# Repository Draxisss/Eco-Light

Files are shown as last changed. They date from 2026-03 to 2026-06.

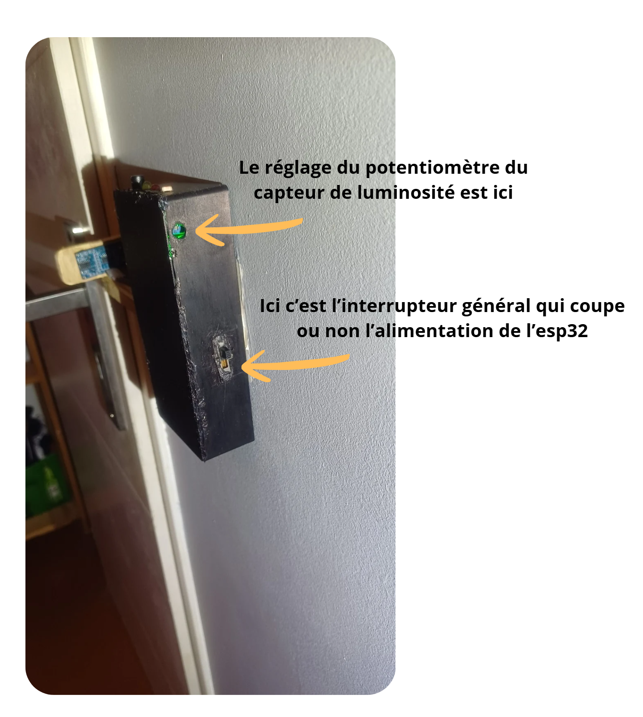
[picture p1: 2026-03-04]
assets/image/lum.png

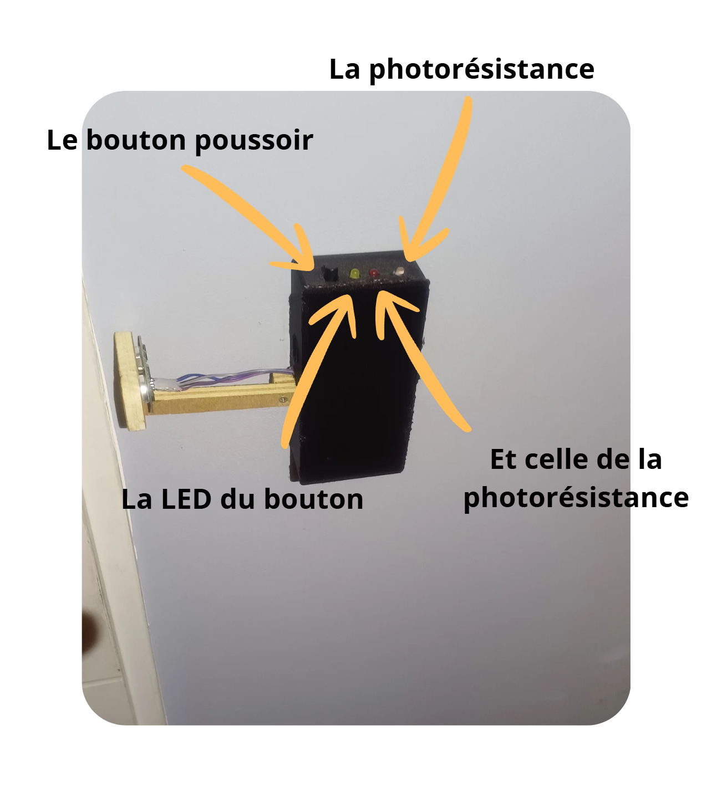
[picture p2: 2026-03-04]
assets/image/comp.png

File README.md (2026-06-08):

# L'Éco'Light 

---

Ceci est ma participation pour le concours Innovez, vous trouverez dans ce dépôt tous les fichiers et explications nécessaires pour comprendre, mettre en place et même juger mon travail si vous faites partie du jury. Voici **l'Éco'Light**.  

La section [montage](#montage) explique comment **vous** pouvez mettre l'Éco'Light chez vous.

## Présentation 

Tout d'abord, l'Éco'Light est un interrupteur autonome et connecté. C'est à dire qu'il remplace un interrupteur classique en lieu et place et surtout dans sa fonction. Pour rapidement voir à quoi il ressemble, il y a la [visualisation 3d](3d/eco-light.stl) 



Lors de la conception de l'Éco'Light, le point de départ était un constat simple : l'interrupteur classique fonctionne bien mais on peut faire **mieux** et quelques limites sont évidentes : le fait d'oublier la lumière allumée en plein jour, ne pas pouvoir allumer les mains prises, l'absence de contrôle à distance et aussi, depuis la crise du Covid-19 où la question de l'hygiène est devenue un sujet central, or l'interrupteur est l'un des objets les plus touchés des espaces partagés, il accumule et transfère donc les microbes. L'Éco'Light est ici une solution parfaite ! Je voulais concevoir l'interrupteur qui réponde à tous ces critères mais aussi qui soit abordable, open-source et fiable, bref qui s'installe comme un interrupteur normal mais fait **bien plus**.

### Contraintes:

- Faire des économies (limiter la possibilité d'allumer la lumière en fonction de la luminosité)
- Pouvoir allumer sans utiliser un bouton physique
- Rendre le tout entièrement connecté et utilisable dans le monde **entier**
- Être compatible au maximum

### Composants, (voir en [détail](#detail-des-composants))

- Le microcontrôleur : un ESP32
- Un capteur à ultrasons : un HC-SR04
- Un relais 5V
- Un module photorésistance
- Un bouton poussoir
- Deux LED (rouge et jaune)

<p align="right">
  
</p>

---

## Fonctionnement

Il suffit d'installer correctement l'Éco'Light à la place de l'interrupteur et via l'application dédiée et ensuite son fonctionnement est très simple : pour changer l'état du plafonnier il faut passer devant le capteur à ultrasons, la distance dépend de ce que l'utilisateur a choisi et la position est ajustable rapidement et à n'importe quel moment.

ultra

En fonction de la luminosité de la pièce, le module photorésistance bloque ou non l'allumage, ou éteint la lumière si elle était allumée lorsque la luminosité a augmenté. Si le module photorésistance est activé alors la LED rouge s'allume pour indiquer à l'utilisateur que le seuil qu'il a fixé est dépassé et qu'il ne peut alors plus allumer la lumière.

lum

On règle ce capteur avec n'importe quel tournevis cruciforme ou plat.

Pour garder la main sur le système le bouton poussoir permet une commande "manuelle", c'est à dire d'allumer ou d'éteindre dans n'importe quelles conditons de luminosité.

comp

### Connectivité 

Faisant partie des contraintes générales qu'en est-il de ce paramètre ?
Et bien un site web permet de surveiller tous les paramètres mais aussi un contrôle total sur le projet **mais pas seulement** on peut aussi avoir accès à d'autres modes de fonctionnement :
- Un mode réveil, qui allume le plafonnier à l'heure choisi
- Un mode cambriolage, qui, si quelque chose passe devant le capteur à ultrasons, envoie une notification et fait clignoter la lumière rapidement
- Un mode plus "fun" que j'ai nommé : mode soirée, qui allume/éteint la lampe au bpm sélectionné



Cette présentation est **personnalisable bien sûr** malgré le fait que ça aurait dû être une application mais j'en reparlerai...

---

### Wiring Diagram 



---
## Composants

| Composant | Quantité |  Prix (EUR) | Lien |
|---|---|---|---|
| Capteur à Ultrasons (HC-SR04) | 1 | 1.40 | https://fr.aliexpress.com/item/1005006039388853.html  |
| Module photorésistance | 1 | 0.94 | https://fr.aliexpress.com/item/1005007038160433.html  |
| Microcontrôleur (ESP32) | 1 | 4.39 | https://fr.aliexpress.com/item/1005008889768599.html |
| Relais | 1 | 1.47 | https://fr.aliexpress.com/item/1005007109343076.html  |
| Bouton poussoir | 1 (20) | 1.31 | https://fr.aliexpress.com/item/4001278311660.html |
| LED | 2 (60) | 2.89 | https://fr.aliexpress.com/item/1005008554748230.html  |
| Interrupteur | 1 (10) | 1.69 | https://fr.aliexpress.com/item/1005007498633815.html  |
| Phase et masse commune | 2 (20) | 1.89 | https://fr.aliexpress.com/item/4000873858801.html |
| Fils de branchements 10cm et 30cm | 40 | 6 en tout | https://fr.aliexpress.com/item/1005002000655439.html  |
| Convertisseur 220v AC vers 5v DC  | 1 | 1.35 | https://fr.aliexpress.com/item/1005001970797548.html  |
| Fils électrique 220v | 1 | 3.59 | https://fr.aliexpress.com/item/1005010779278423.html  |
| Connecteur Wago | 3 | 1.73 | https://fr.aliexpress.com/item/1005006963063019.html  |
| Vis (M4x30, Countersunk head) | 2 (10) | 3.09 | https://fr.aliexpress.com/item/1005007129209802.html  |
| Écrou | 2 (50) | 2.44 | https://fr.aliexpress.com/item/1005010329406193.html  |  
| Résistances | 2 (20) | 0.99 | https://fr.aliexpress.com/item/1005006424279944.html |
| Total | | 35 | C'est seulement si vous achetez toutes les pièces, on peut faire de la récup sur certain composants  |

Pour ma part j'ai réutilisé le convertisseur 220V AC vers 5V DC d'un chargeur, le bouton poussoir d'un petit appareil (PS : un jouet pour enfant, peut-être un dinosaure électronique je ne me souviens plus très bien), les leds d'un jouet pour bébé, les résistances d'un autre projet et les fils d'un starter pack arduino.

**PS :** Les quantités entre parenthèses sont les quantités minimum disponible pour ce produit. Vous pouvez très bien adapter du matériel que vous avez déjà, j'ai simplement mis tout les éléments nécessaires a la conception de l'Éco'Light. Les liens proviennent tous d'aliexpress (plus simple pour l'électronique donc j'ai continué sur ma lancée) mais ils pourront malheureusement devenir invalides si je ne les verifie et actualise pas.
 
### Pour les retrouver vous même : 

- Capteur à Ultrasons : HC-SR04
- Module photorésistance : LDR, module photorésistance, sortie digitale
- Microcontrôleur : ESP32, module devkit, Wi-Fi/Bluetooth
- Relais : module relais, 5 V, 1 canal
- Bouton poussoir : bouton poussoir, 8-10mm, bistable/à verrouillage
- LED : LED 5 mm
- Interrupteur :  2.3 x 0.75 x 1.7cm environ
- Phase et masse commune : Board Pin Header que vous soudez ensemble
- Fils de branchements 10 cm et 30 cm : femelle/femelle
- Convertisseur 220 V → 5 V : module AC-DC, 5w
- Fils électrique 220 V : awg14-15
- Connecteur Wago triple
- Vis : M4x30, tête fraisée
- Écrou : écrou M4, 2-2.5mm d'épaisseur
- Résistance : 150-220Ω

## Montage
Matériel nécessaire : 
- tous les composants
- un tournevis cruciforme
- un fer à souder (aucune soudure n'est difficile)
- un pistolet à colle
- une pince ou quelque chose de similaire et une clé Allen pour les vis du bras
- et un peu d'huile de coude

Une fois toutes les pièces réunies, vous pouvez commencer à construire **votre** Éco'Light ! 

Il vous faudra imprimer en 3d le fichier [suivant](3d/eco-light.stl). **Attention** ne surtout pas imprimer les deux corps, c'est seulement pour choisir entre un interrupteur à gauche ou à droite. De même avec les "bras" pour le capteur à ultrasons, imprimez en un seul, j'ai modélisé 3 tailles : 8, 10 et 12cm.

Il faut ensuite récupérer le [code](code/code_esp32.ino) pour l'ESP32 et le flasher sur votre microcontrôleur via Arduino IDE (un logiciel de programmation pour tout ces petits microcontrôleur)

Réalisez le montage ci-dessous soit directement dans le boîter fraichement imprimé si vous êtes confiant soit sur une breadboard pour être sûr : 

| Nom | Pin | "Complément" |
|---|-----|---|
| Trig | 19  | Vcc + Gnd (capteur à ultrasons) |
| Echo | 18  | " " |
| Led jaune | 33  | Gnd |
| Led rouge | 26  | Gnd |
| Relai | 23  | Vcc + Gnd |
| Photorésistance | 27  | Vcc + Gnd |
| Bouton poussoir | 5 | Gnd |
| Plus généralement : VCC | 5V  | |
| GND | Gnd | |
| | | |

Pour les leds, pensez bien à rajouter une résistance, sinon vous risquez de la griller.

Malheureusement n'ayant aucune connaissance en PCB je n'ai pas pu en faire une mais si ce projet marche je promet qu'elle sortira et alors on gagnera en taille de boitier et en facilité de montage.

Une fois que vous êtes sur du bon fonctionnement du projet alors vous pouvez passez au collage où le but va être de tout faire rentrer dans cette petite boîte. La mission peut être un peu technique mais devrait finir par ressembler à ça :

elec

À partir de là vous pouvez passer à la catégorie **installation** pour fixer et démarrer l'Éco'Light.

---
## Installation 

Très simplement vous allez le fixer à la place de l'interrupteur : l'Éco'Light respecte les dimensions standards, entraxe des vis de fixations de 60 mm (boite Ø67 mm).
Il n'y a que le câblage qui change puisqu'il faut alimenter le microcontrôleur en électricité. Rassurez-vous le travail à faire est minime : 



On a donc ça du côté du boitier :



Si on représente tout schématiquement pour mieux comprendre la situation et éclaircir un petit peu les choses 



 Aucune compétence en électricité n'est nécessaire même votre grand-mère pourrait le faire c'est dire ! (ps: je doute que beaucoup de grand-mères utilisent Github).
 Bref plutôt dire qu'il ne faut pas du tout s'inquiéter sur ce point.

 Ensuite vous vissez le tout (2 vis) et il n'y a plus qu'à allumer la machine via l'interrupteur latéral !

 Pour ensuite, magie, vous connecter à l'ESP32 avec votre téléphone pour finaliser la mise en place. Le but de cette application est d'informer le microcontrôleur de vos préférences (mdp wifi, distance détection...), il suffit de suivre ces étapes :

 

 (à chaque fois il y aura la fenêtre d'erreur associée à l'étape correspondante pour comprendre si vous avez un problème)

 Page d'accueil donc, avant il faut appairer l'ESP32 avec votre téléphone (Paramètres → Connexions → Bluetooth → Sélectionner appareil (Éco'Light) → Appairer), après cette étape de complétée et un temps de chargement plus ou moins long :
 

(Le bouton Reset sert si vous avez un problème durant le processus (freeze, erreur...), il redémarre l'ESP32 et vous renvoie à la page d'accueil)

 Vous arrivez sur :

 

Il faut donc choisir son réseau wifi et indiquer le mot de passe pour que l'ESP32 ait accès à internet

Pour ensuite choisir la distance de détection du capteur à ultrasons (votre choix dépendra de l'emplacement de votre interrupteur, de la position de votre capteur mais surtout si vous voulez qu'il vous détecte quand vous passez vous ou votre main. Par exemple je l'ai réglé moi pour que, quand je circule, le capteur ne détecte rien mais quand je me rapproche ou passe ma main devant il allume la lumière (on peut donc rentrer et sortir sans changer l'état de la lumière). C'est plus agréable je trouve surtout si vous vivez à plusieurs, qu'il y a des va et vient dans la pièce concernée car on peut quand même allumer la lumière les bras chargés). 



(Ps : moi comme référence je l'ai donc réglé à 13cm avec un interrupteur plutôt proche du cadre de porte)

Vient ensuite la partie "API", créez un compte sur [Adafruit](https://io.adafruit.com) et rentrez vos informations (le nom d'utilisateur et la clé API peuvent être trouvés en cliquant sur l'icone de clé en haut à droite) et vous les rentrez ensuite ci-dessous :



Il faudra ensuite respecter le tableau suivant lors de la création des feeds et du dashboard sur le site d'adafruit où vous irez ensuite après la mise en place de l'Écolight (à vous de personnaliser votre expérience).

| Fonction | Nom du feed  | Objet associé sur le dashboard |
|---|---|---|
| Gérer l'allumage | lampe | Toggle |
| Gérer le mode cambiolage | cambriolage  | Toggle |
| Gérer le message d'alerte | notif | Text (Show icon avec exclamation-triangle) |
| Gérer le mode réveil | reveil | Toggle |
| Gérer l'heure du réveil | reveil heure | Text |
| Gérer le mode "soirée" | soiree | Toggle |
| Gérer les bpm du mode "soirée"  | soiree bpm | Text |

Pour rentrer l'heure pour le réveil dans le bloc texte le format attendu est le suivant : XX:XX (Ex: 7:15, 12:28, 22:55)



Si tout s'est bien passé alors cette page apparait et vous êtes prêt à utiliser l'Éco'Light pour la première fois !
Maintenant que vous êtes sûr du bon fonctionnement du projet vous pouvez alors coller le couvercle à la colle chaude (un léger filet suffit) et profiter pleinement de votre Éco'Light à la maison.

Si jamais un problème arrive ou vous voulez changer de taille de bras et aussi de distance de détection : relancez l'application et coupez et rallumez l'ESP32

---

Je voulais juste faire un point sur l'interface utilisateur, je trouve le dashboard adafruit très limitant (même moche, faut le dire un jour) et j'avais à la base créé une application beaucoup plus agréable que je veux quand même partager malgré le fait que l'API d'adafruit ne m'a pas permis de trouver une solution (impossible de s'abonner à un feed sur adafruit depuis l'application, pour celles ou ceux qui demenderaient).



Donc voilà quelque chose de beaucoup plus attrayant mais que je n'ai pu finaliser malgré des heures de travail...

---

# Conclusion

Je me suis régalé pendant toute la conception, la création, le travail de recherche, la mise en forme ou encore les soirée passées à retourner dans tous les sens un problème que je n'arrivais pas à résoudre sur ce projet pour enfin aboutir. Je suis tellement heureux de pouvoir arriver le soir chez et de n'avoir plus, dans un coin de ma tête, une petite voix me disant de toujours peaufiner un détail que personne ne verra... Mais finalement en plus de l'aboutissement, ça ne serait pas ça qui compteraient le plus, toutes les galères rencontrées, non ?

J'ai bien sur quelques idées d'amélioration en tête et je serais ravi de vous les partager. En tout cas j'espère (si vous êtes arrivé jusque là) que ce projet vous a plu et j'espère surtout vous avoir convaincu !

PS : je n'ai jamais eu de retour extérieur à ce projet mis à part la famille et des amis proches et je pense que c'est toujours extrêmmement intéressant d'en recevoir. Sentez vous libre de partager vos avis et sentiments.
cameosauvageon@mail.com

[Présentation en vidéo du projet](https://youtu.be/p83ESVzQn0w)

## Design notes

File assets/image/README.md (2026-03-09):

# Disclaimer

---

Les photos présentées sont celles de mon prototype installé fonctionnel mais comme n'ayant pas d'imprimante 3d et vivant dans la France à Macron et bien je n'ai pas pu tout réimprimer en 3d. Par contre tout les fichiers sont bon et permettent la création d'un modèle vraiment fini sans les traces de colle ou autres désagréments.

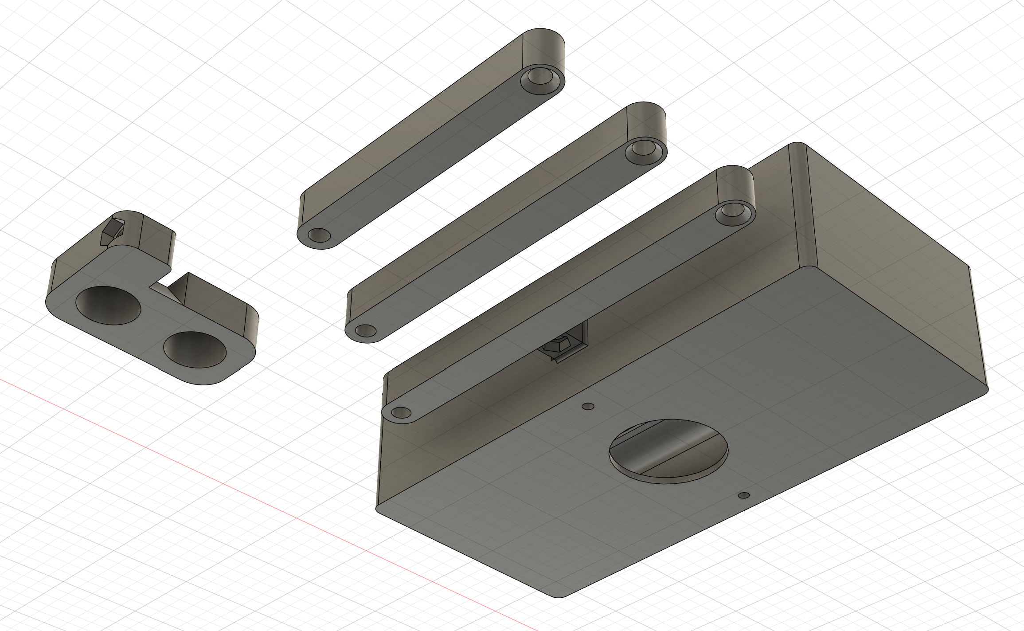
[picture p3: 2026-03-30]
assets/image/Capture d’écran 2026-03-30 215438.png

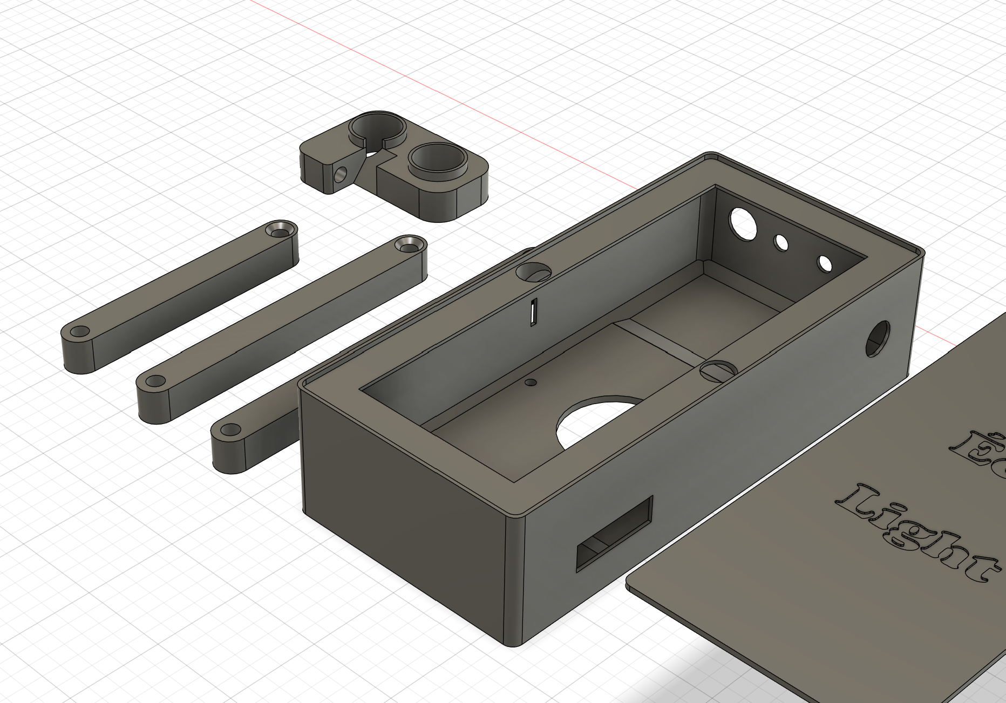
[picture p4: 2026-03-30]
assets/image/Capture d’écran 2026-03-30 215513.png

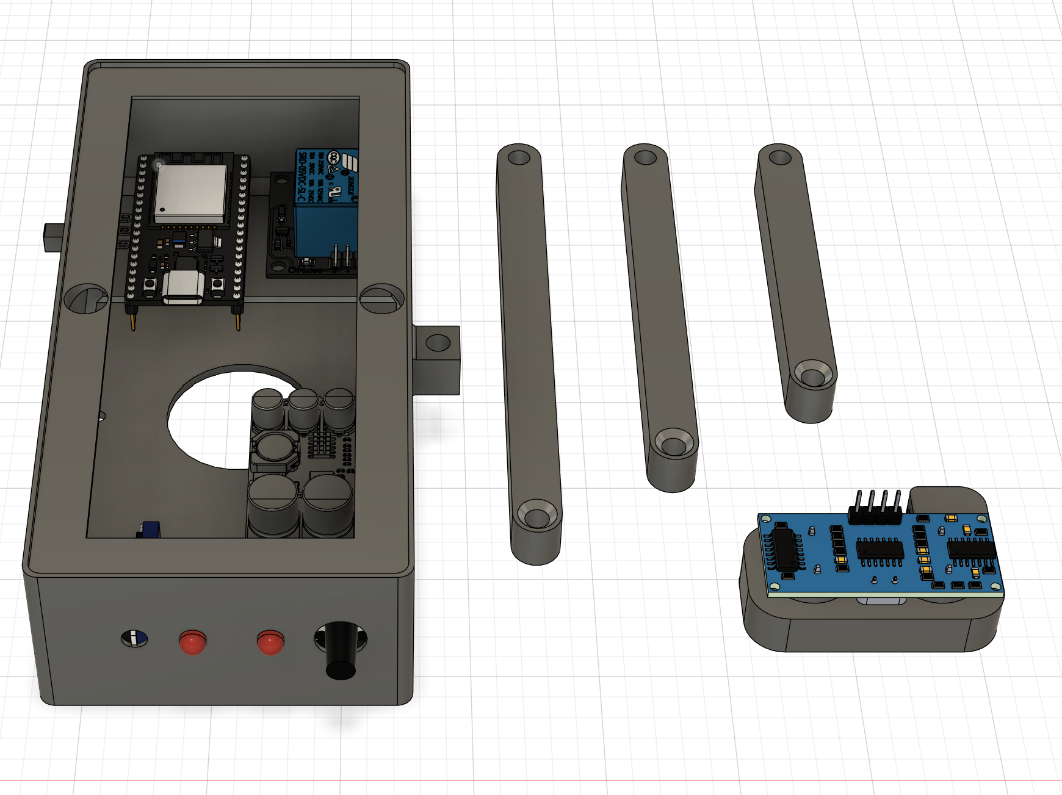
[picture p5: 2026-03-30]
assets/image/Capture d’écran 2026-03-30 232008.png

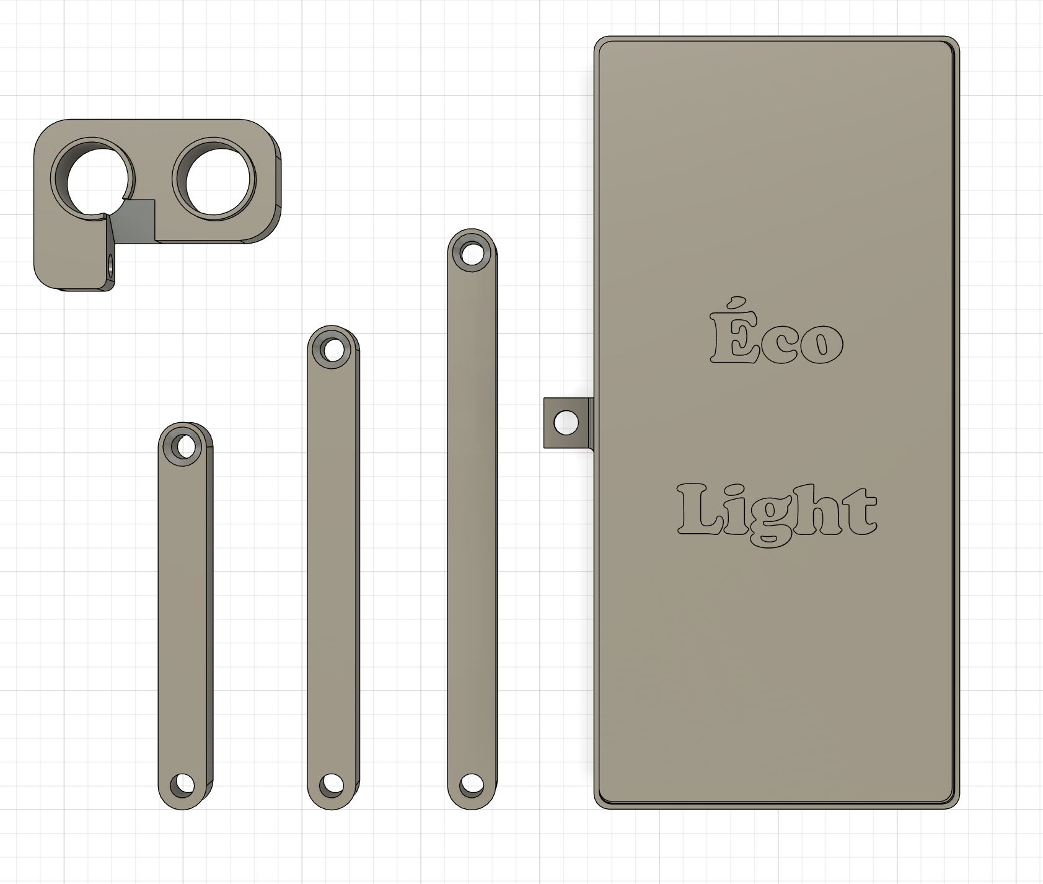
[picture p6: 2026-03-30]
assets/image/Capture d’écran 2026-03-30 215237.png

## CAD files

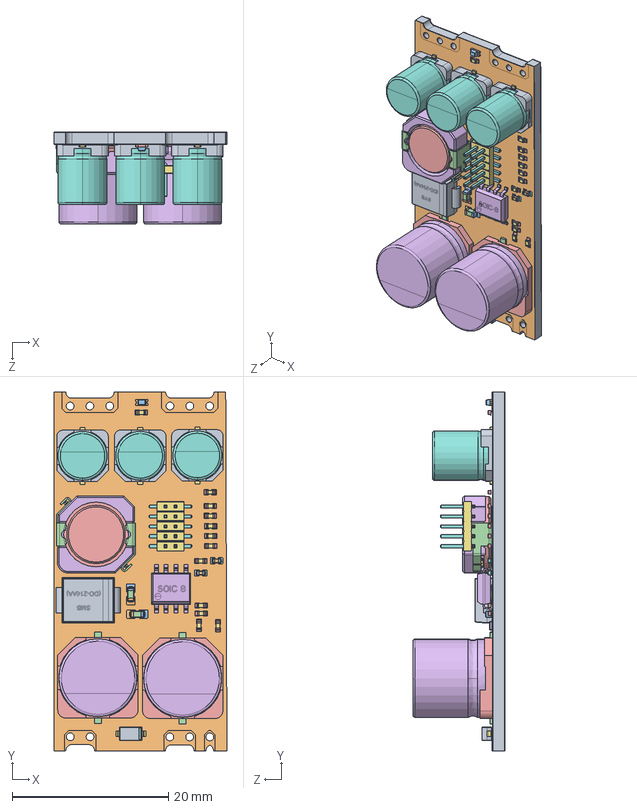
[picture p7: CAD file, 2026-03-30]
assets/Components/Assemblage alim 3 multi choix.STEP
22.2 x 46.0 x 11.9 mm
PCB
Piste face Avant
Piste face Arrière
CAPAE1030X1050N-(G).stp x 2
CAPAE660X800N-(D8).stp x 3
0603 Chip SMD LED (1.6x0.8mm).step
soic8_p1-27_l5-0_w4-0.stp
SOD-123
CDRH104R.step
BaseBody.step
Pin1Body.step
Pin2Body.step
Pin3Body.step
Pin4Body.step
Pin5Body.step
Pin6Body.step
Pin7Body.step
Pin8Body.step
Pin9Body.step
Pin10Body.step
S3M(SMB).step
Cap & pads (1608).step x 2
Pin1.step x 12
Pin2.step x 12
CeramicBody.step x 12
Coating.step x 12
Cap & pads (1005).step x 2

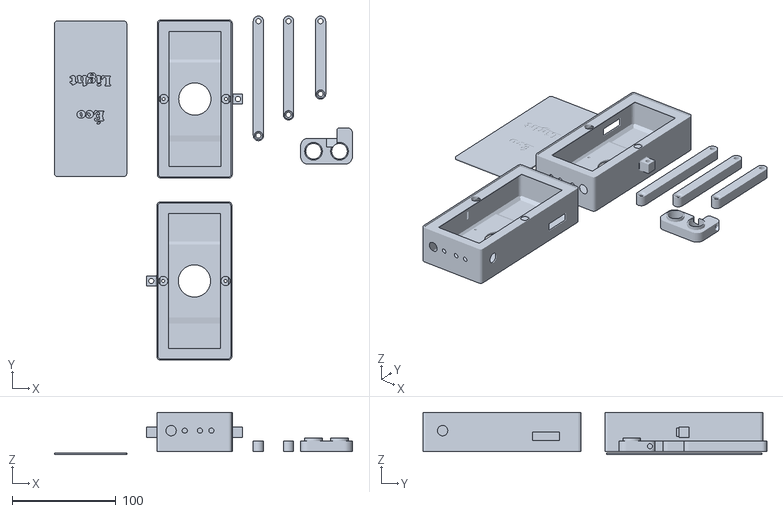
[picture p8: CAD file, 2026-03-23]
3d/eco-light.stl
286.6 x 330.8 x 40.5

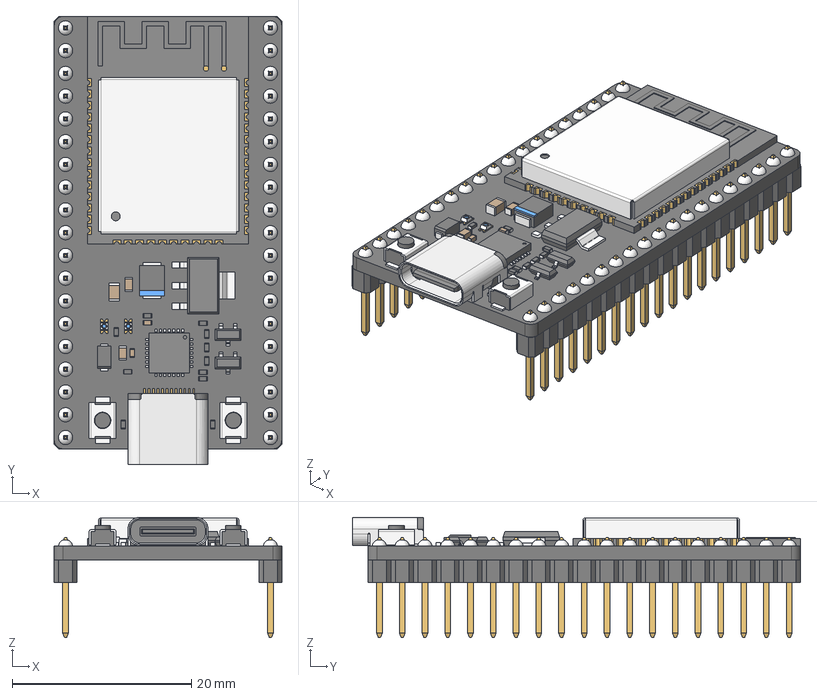
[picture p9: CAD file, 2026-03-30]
assets/Components/ESP32 WROOM.step
25.4 x 50.0 x 13.4 mm

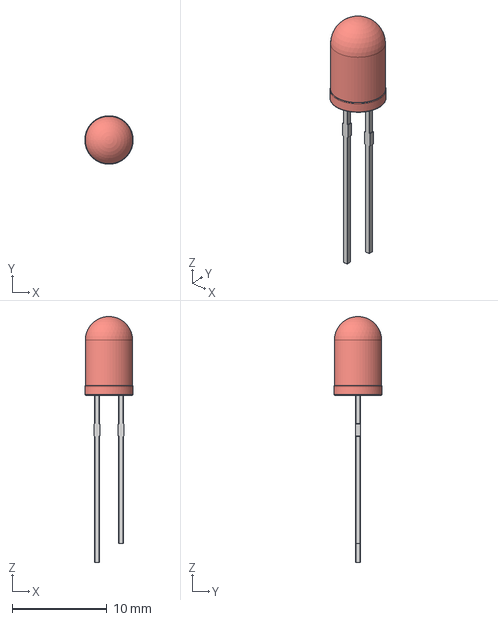
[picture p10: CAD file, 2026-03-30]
assets/Components/LED_5mm.step
5.10 x 5.10 x 25.9 mm

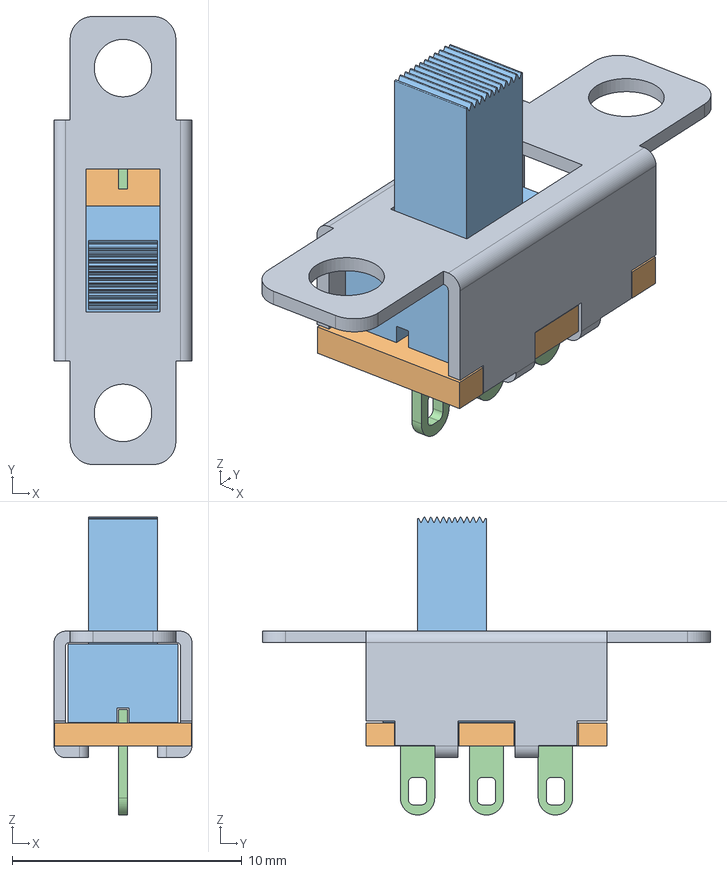
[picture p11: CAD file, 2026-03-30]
assets/Components/switch_SS12F15G5.step
6.00 x 19.5 x 13.0 mm
metal_sw
boad_sw
move_sw
pin_sw
pin_sw001
pin_sw002

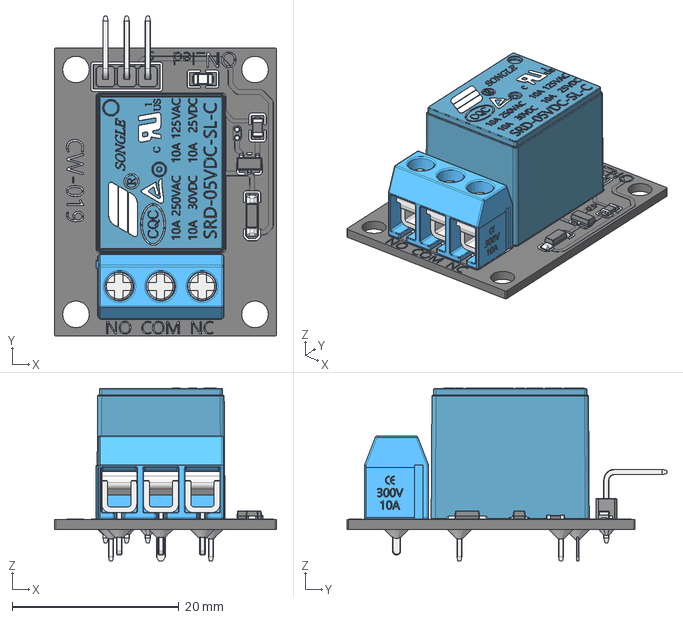
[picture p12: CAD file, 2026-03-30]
assets/Components/CW-019.stp
26.7 x 38.4 x 20.8 mm

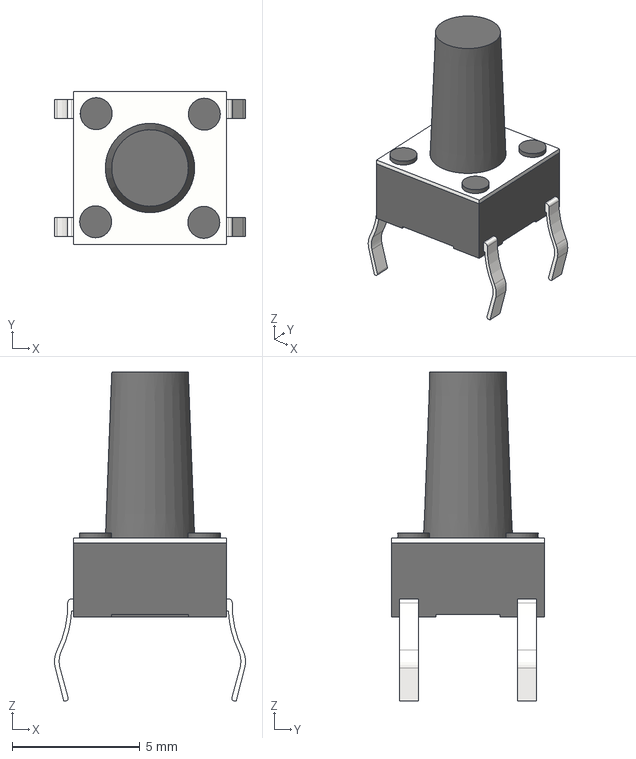
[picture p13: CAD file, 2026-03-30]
assets/Components/push_switch_small.step
7.48 x 6.00 x 12.9 mm

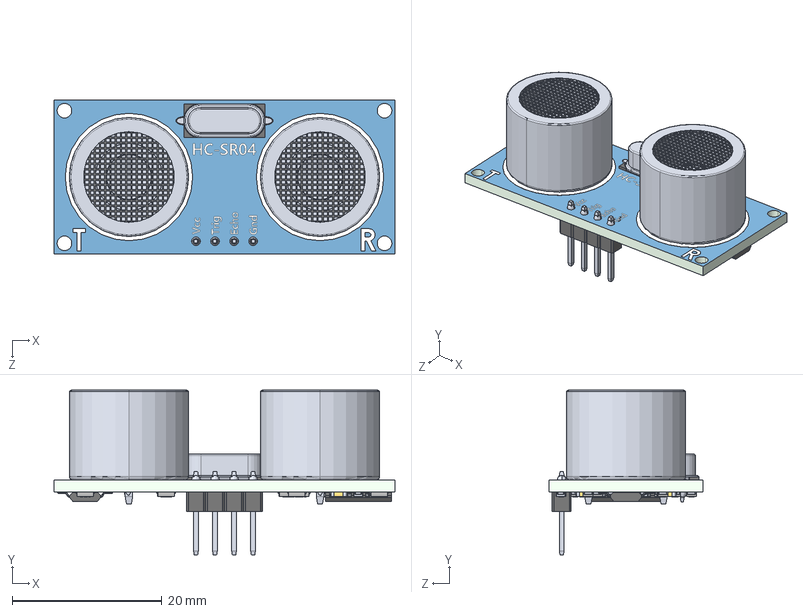
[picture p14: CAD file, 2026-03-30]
assets/Components/HC-SR04.STEP
45.5 x 21.9 x 20.5 mm
HC-SR04board
solder x 10
Emitter x 2
CrystalOscillator
smdChip14pin x 2
smdChip16pin
smdceramiccapacitor x 7
smdResistor753 x 3
smdResistor392
smdResistor103 x 6
smdResistor124 x 2
smdResistor335
smdResistor102
smdResistor563
smdResistor622
smdResistor412
headerMale x 4

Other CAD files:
3d/eco-light_final_with_electronic.f3z
3d/eco-light_fusion360.f3d

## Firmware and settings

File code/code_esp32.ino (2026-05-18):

#include <WiFi.h> 
#include "WiFiClientSecure.h"
#include "Adafruit_MQTT.h"
#include "Adafruit_MQTT_Client.h"
#include "time.h"
#include "BluetoothSerial.h"
#include "Ultrasonic.h"

BluetoothSerial SerialBT;

/************************* adafruit io setup *********************************/

#define AIO_SERVER "io.adafruit.com"
#define AIO_SERVERPORT 1883

WiFiClient client;

char pseudo[50];
char key[50];
Adafruit_MQTT_Client mqtt(&client, AIO_SERVER, AIO_SERVERPORT, pseudo, key);

/****************************** feeds  setup ***************************************/
char path_lampe[60], path_cambriolage[60], path_soiree[60], path_bande_led[60], path_reveil_heure[60], path_soiree_bpm[60], path_notif[60], path_reveil[60];

Adafruit_MQTT_Subscribe lampeSub = Adafruit_MQTT_Subscribe(&mqtt, path_lampe); // cette ligne sert a s'abonner a un feed pour recevoir des donnees via mqtt
Adafruit_MQTT_Publish lampePub = Adafruit_MQTT_Publish(&mqtt, path_lampe); // celle la pour envoyer et ecrire sur un feed

Adafruit_MQTT_Subscribe cambriolageSub = Adafruit_MQTT_Subscribe(&mqtt, path_cambriolage);
Adafruit_MQTT_Publish cambriolagePub = Adafruit_MQTT_Publish(&mqtt, path_cambriolage);

Adafruit_MQTT_Subscribe soireeSub = Adafruit_MQTT_Subscribe(&mqtt, path_soiree);
Adafruit_MQTT_Publish soireePub = Adafruit_MQTT_Publish(&mqtt, path_soiree);

Adafruit_MQTT_Subscribe bande_ledSub = Adafruit_MQTT_Subscribe(&mqtt, path_bande_led);
Adafruit_MQTT_Publish bande_ledPub = Adafruit_MQTT_Publish(&mqtt, path_bande_led);

Adafruit_MQTT_Subscribe reveil_heureSub = Adafruit_MQTT_Subscribe(&mqtt, path_reveil_heure);
Adafruit_MQTT_Publish reveil_heurePub = Adafruit_MQTT_Publish(&mqtt, path_reveil_heure);

Adafruit_MQTT_Subscribe soiree_bpmSub = Adafruit_MQTT_Subscribe(&mqtt, path_soiree_bpm);
Adafruit_MQTT_Publish soiree_bpmPub = Adafruit_MQTT_Publish(&mqtt, path_soiree_bpm);

Adafruit_MQTT_Subscribe notifSub = Adafruit_MQTT_Subscribe(&mqtt, path_notif);
Adafruit_MQTT_Publish notifPub = Adafruit_MQTT_Publish(&mqtt, path_notif);

Adafruit_MQTT_Subscribe reveilSub = Adafruit_MQTT_Subscribe(&mqtt, path_reveil);
Adafruit_MQTT_Publish reveilPub = Adafruit_MQTT_Publish(&mqtt, path_reveil);

/*************************** pins et variables utilisés dans le code ************************************/
bool initialisation1 = false;
bool initialisation2 = false;

// tout les pins 
Ultrasonic ultrasonic1(19, 18); // Trig = 19, Echo = 18
int pin_led = 33;
int pin_bouton = 5;
int pin_led2 = 26;
int pin_relay = 23;
int pin_luminosity = 27;
bool bouton_appuye_previous = false;

//capteur ultrasons
int distance_detection_ultrasonic = 30;
bool etat_lumiere = false;
bool etat_capteur_ultrason = false;
bool interLum = false;
bool interBut = false;
bool varLum = false;
unsigned long lastMqttPing = 0;

// variables qui servent a verifier le precedent message envoyé pour ne pas dépasser la limite par minute de adafruit
const char* etat_lumiere_str_previous = "";
const char* reveil_str_previous = "";
const char* cambriolage_str_previous = "";
const char* soiree_str_previous = "";
const char* bande_led_str_previous = "";

// cambriolage
bool cambriolage = false;
int delay_cambriolage = 500;
unsigned long previous_delay = 0;
bool cambriolageDetect = false;
bool cambriolage_previous = true;
bool notif_state = false;
bool notif_state_previous = false;

bool soiree = false;

bool bande_led = false; // toutes les appellations a bande led sont du parce que je voulais rajouter la possibilité de mettre une bande led en plus du plafonnier principal mais je n'ai pas reussi a flasher un nouveau firmware dans mes bande led donc c'est aussi une partie du projet inachevée

// reveil
bool reveil = false;
bool reveilLum = false;
int reveil_minute = 0;
int reveil_heure = 0;
const char* timezone = "CET-1CEST,M3.5.0/2,M10.5.0/3"; // c'est ce qui gere les passage heure d'hiver/ heure d'ete
const char* ntpServer = "fr.pool.ntp.org";

int soiree_bpm = 100;
int delay_bpm = 60000/soiree_bpm;
unsigned long previous_delay_bpm = 0;

char notif[64] = "";

bool delai = false;

// les fonction callback sont la pour savoir quoi faire quand un nouveau message apparait sur le feed
void lampeCallback(char* message, uint16_t len) {
  char messageBuffer[40];
  snprintf(messageBuffer, sizeof(messageBuffer), "lampe status is :: %s, len :: %u", message, len);
  Serial.println(messageBuffer);
  if (strcmp(message, "ON") == 0) {
    Serial.println("Turning ON lampe");
    digitalWrite(pin_relay, LOW);
    Serial.println("relay on");
    etat_lumiere = true;
  } else {
    Serial.println("Turning OFF lampe");
    digitalWrite(pin_relay, HIGH);
    Serial.println("relay off");
    etat_lumiere = false;
  }
}

void cambriolageCallback(char* message, uint16_t len) {
  char messageBuffer[40];
  snprintf(messageBuffer, sizeof(messageBuffer), "cambriolage status is :: %s, len :: %u", message, len);
  Serial.println(messageBuffer);
  if (strcmp(message, "ON") == 0) {
    cambriolage = true;
  } else {
    cambriolage = false;
  }
}

void soireeCallback(char* message, uint16_t len) {
  char messageBuffer[40];
  snprintf(messageBuffer, sizeof(messageBuffer), "soiree status is :: %s, len :: %u", message, len);
  Serial.println(messageBuffer);
  if (strcmp(message, "ON") == 0) {
    soiree = true;
  } else {
    soiree = false;
  }
}

void bandeLedCallback(char* message, uint16_t len) {
  char messageBuffer[40];
  snprintf(messageBuffer, sizeof(messageBuffer), "bande led status is :: %s, len :: %u", message, len);
  Serial.println(messageBuffer);
  if (strcmp(message, "ON") == 0) {
    bande_led = true;
  } else {
    bande_led = false;
  }
}

void reveilHeureCallback(char* message, uint16_t len) {
  char messageBuffer[40];
  snprintf(messageBuffer, sizeof(messageBuffer), "reveil heure status is :: %s, len :: %u", message, len);
  Serial.println(messageBuffer);

  sscanf(message, "%d:%d", &reveil_heure, &reveil_minute);
  Serial.print(reveil_heure);
  Serial.print(":");
  Serial.println(reveil_minute);

}

void soireeBpmCallback(char* message, uint16_t len) {
  char messageBuffer[40];
  snprintf(messageBuffer, sizeof(messageBuffer), "soiree bpm status is :: %s, len :: %u", message, len);
  Serial.println(messageBuffer);
  soiree_bpm = atoi(message);
  Serial.println(soiree_bpm);
}

void notifCallback(char* message, uint16_t len) {
  char messageBuffer[64];
  snprintf(messageBuffer, sizeof(messageBuffer), "notif status is :: %s, len :: %u", message, len);
  Serial.println(messageBuffer);


}

void reveilCallback(char* message, uint16_t len) {
  char messageBuffer[64];
  snprintf(messageBuffer, sizeof(messageBuffer), "reveil status is :: %s, len :: %u", message, len);
  Serial.println(messageBuffer);
  if (strcmp(message, "ON") == 0) {
    reveil = true;
  } else {
    reveil = false;
  }

}

// la fonction qui permet de publier surles feed sans depasser les limite de message par minute
void indicatorPublish() {

  const char* etat_lumiere_str = etat_lumiere ? "ON" : "OFF";
  if (strcmp(etat_lumiere_str_previous, etat_lumiere_str) != 0) {
    lampePub.publish(etat_lumiere_str);
    etat_lumiere_str_previous = etat_lumiere_str;
  }

  const char* reveil_str = reveil ? "ON" : "OFF";
  if (strcmp(reveil_str_previous, reveil_str) != 0) {
    reveilPub.publish(reveil_str);
    reveil_str_previous = reveil_str;
  }

  const char* cambriolage_str = cambriolage ? "ON" : "OFF";
  if (strcmp(cambriolage_str_previous, cambriolage_str) != 0) {
    cambriolagePub.publish(cambriolage_str);
    cambriolage_str_previous = cambriolage_str;
  }

  const char* soiree_str = soiree ? "ON" : "OFF";
  if (strcmp(soiree_str_previous, soiree_str) != 0) {
    soireePub.publish(soiree_str);
    soiree_str_previous = soiree_str;
  }

  const char* bande_led_str = bande_led ? "ON" : "OFF";
  if (strcmp(bande_led_str_previous, bande_led_str) != 0) {
    bande_ledPub.publish(bande_led_str);
    bande_led_str_previous = bande_led_str;
  }

}


void MQTT_connect() {
  int8_t ret;
  if (mqtt.connected()) {
    return;
  }
  Serial.print("Connecting to MQTT... ");
  uint8_t retries = 20;
  while ((ret = mqtt.connect()) != 0) {  
    Serial.println(mqtt.connectErrorString(ret));
    Serial.println("Retrying MQTT connection in 5 seconds...");
    mqtt.disconnect();
    delay(2000); 
    retries--;
    if (retries == 0) {
      SerialBT.print("XJ");
      esp_restart();
    }
  }
  Serial.println("MQTT Connected!");
}


void setup() {
  Serial.begin(115200);
  delay(10);
  pinMode(pin_led, OUTPUT); 
  pinMode(pin_led2, OUTPUT);
  pinMode(pin_relay, OUTPUT);
  pinMode(pin_luminosity, INPUT);
  pinMode(pin_bouton, INPUT_PULLUP); //assignation des modes aux pins

  Serial.println(F("Concours Innovez version finale"));

  // connecter au wifi
  SerialBT.begin("Eco'light");  // Nom visible en Bluetooth
  
  WiFi.mode(WIFI_STA);
  WiFi.disconnect();
  delay(100);
  Serial.println();

  // Attacher les fonctions de callback
  lampeSub.setCallback(lampeCallback);
  cambriolageSub.setCallback(cambriolageCallback);
  soireeSub.setCallback(soireeCallback);
  bande_ledSub.setCallback(bandeLedCallback);
  reveil_heureSub.setCallback(reveilHeureCallback);
  soiree_bpmSub.setCallback(soireeBpmCallback);
  notifSub.setCallback(notifCallback);
  reveilSub.setCallback(reveilCallback);

}

// boucle principale
void loop() {
  if (SerialBT.hasClient()) {
    if (!initialisation1) {
      Serial.println("Scan start");
      // WiFi.scanNetworks retourne le nombre de réseau trouvé.
      int n = WiFi.scanNetworks();
      Serial.println("Scan done");
      delay(1000);
      for (int i = 0; i < n; ++i) {
        String ssid = WiFi.SSID(i);
        int len = ssid.length();

        // convertir la longueur en chaîne de 2 chiffres
        if (len < 10) {
          SerialBT.print("0");  // ajouter un 0 devant
        }
        SerialBT.print(len);     // envoyer la longueur (ex : "05")
        Serial.println(len);
        delay(500);
        SerialBT.print(ssid);    // puis le SSID brut
        Serial.println(ssid);
        delay(500);
        Serial.println(i);
      }
      SerialBT.print("EN");
      Serial.println("EN");
      WiFi.scanDelete();
      initialisation1 = true;
      }
    }
    
      
    if (SerialBT.available()) {
      if (!initialisation2) {

        String ssid = SerialBT.readStringUntil('\n');
        ssid.trim();  // supprime les espaces ou retours à la ligne
        // on vérifie si le premier caractère est '/'
        if (ssid.length() > 0 && ssid.charAt(0) == '/') {
        ssid.remove(0, 1); // supprime le premier caractère
        }

        Serial.println();
        Serial.print("Connecting to ");
        Serial.println(ssid);

        while (!SerialBT.available()) {
          delay(10);
        }
        String password = SerialBT.readStringUntil('\n');
        password.trim();

        Serial.print("Password: ");
        Serial.println(password);

        // connexion WiFi
        WiFi.begin(ssid.c_str(), password.c_str());

        int attempts = 0;
        while (WiFi.status() != WL_CONNECTED && attempts < 20) {
          delay(500);
          Serial.print(".");
          attempts++;
        }

        if (WiFi.status() == WL_CONNECTED) {
          configTzTime(timezone, ntpServer); // configurer l'heure 
          Serial.println("WiFi connected");
          Serial.println("IP address: ");
          Serial.println(WiFi.localIP()); 
          SerialBT.print("AB");  // confirmer à App Inventor
          digitalWrite(pin_led2, HIGH);
          digitalWrite(pin_led, HIGH);
          delay(1000);
          digitalWrite(pin_led2, LOW);
          digitalWrite(pin_led, LOW);
          delay(500);
          digitalWrite(pin_led2, HIGH);
          digitalWrite(pin_led, HIGH);
          delay(1000);
          digitalWrite(pin_led2, LOW);
          digitalWrite(pin_led, LOW);
          delay(500);
        } else {
          Serial.println("\nÉchec de connexion WiFi.");
          SerialBT.print("XI"); // envoyer l'erreur a App inventor
        }

        while (!SerialBT.available()) {
          delay(10);
        }
        String pseudostr = SerialBT.readStringUntil('\n');
        pseudostr.trim();
        pseudostr.toCharArray(pseudo, sizeof(pseudo));

        snprintf(path_lampe, sizeof(path_lampe), "%s/feeds/lampe", pseudo);
        snprintf(path_cambriolage, sizeof(path_cambriolage), "%s/feeds/cambriolage", pseudo);
        snprintf(path_soiree, sizeof(path_soiree), "%s/feeds/soiree", pseudo);
        snprintf(path_bande_led, sizeof(path_bande_led), "%s/feeds/bande-led", pseudo);
        snprintf(path_reveil_heure, sizeof(path_reveil_heure), "%s/feeds/reveil-heure", pseudo);
        snprintf(path_soiree_bpm, sizeof(path_soiree_bpm), "%s/feeds/soiree-bpm", pseudo);
        snprintf(path_notif, sizeof(path_notif), "%s/feeds/notif", pseudo);
        snprintf(path_reveil, sizeof(path_reveil), "%s/feeds/reveil", pseudo);

        // s'abonner à chaque feed
        mqtt.subscribe(&lampeSub);
        mqtt.subscribe(&cambriolageSub);
        mqtt.subscribe(&soireeSub);
        mqtt.subscribe(&bande_ledSub);
        mqtt.subscribe(&reveil_heureSub);
        mqtt.subscribe(&soiree_bpmSub);
        mqtt.subscribe(&notifSub);
        mqtt.subscribe(&reveilSub);

        while (!SerialBT.available()) {
          delay(10);
        }
        String keystr = SerialBT.readStringUntil('\n');
        keystr.trim();  
        keystr.toCharArray(key, sizeof(key));

        MQTT_connect();

        if (mqtt.connected()) {
          Serial.println("Adafruit connecté");
          Serial.printf("Pseudo: %s | Key: %s\n", pseudo, key);
          SerialBT.print("AC");  // confirmer à App Inventor
          digitalWrite(pin_led2, HIGH);
          digitalWrite(pin_led, LOW);
          delay(1000);
          digitalWrite(pin_led2, LOW);
          digitalWrite(pin_led, HIGH);
          delay(500);
          digitalWrite(pin_led2, HIGH);
          digitalWrite(pin_led, LOW);
          delay(1000);
          digitalWrite(pin_led2, LOW);
          digitalWrite(pin_led, HIGH);
          delay(1000);
          digitalWrite(pin_led2, LOW);
          digitalWrite(pin_led, LOW);
          delay(500);
        } else {
          Serial.println("\nÉchec de connexion MQTT");
          SerialBT.print("XJ"); // envoyer l'echec sinon
        }       

        while (!SerialBT.available()) {
          delay(10);
        }
        String ultra = SerialBT.readStringUntil('\n');
        ultra.trim(); 
        distance_detection_ultrasonic = ultra.toInt(); 

        initialisation2 = true;
      }
    }
  
  if (SerialBT.hasClient()) {
    if (SerialBT.available()) {
      if (SerialBT.read() == 'a') {
        ESP.restart();
      }
    }
  }
  if (initialisation2)  {
    if (WiFi.status() == WL_CONNECTED) {
      MQTT_connect();
      mqtt.processPackets(50);
    } else {
      Serial.println("WiFi non connecté, MQTT ignoré");
    }

    indicatorPublish();

    if (millis() - lastMqttPing >= 10000) {
      lastMqttPing = millis();
      mqtt.ping();
    }
    
/****************************** debut du code pour gerer seulement l'interrupteur et non la connectivite ***************************************/
    delai = false;
    int mesure_ultrasons = ultrasonic1.Ranging(CM);
    bool bouton_appuye = digitalRead(pin_bouton) == LOW; 
    bool luminosite_importante = digitalRead(pin_luminosity) == LOW;

    if (bouton_appuye) {
      interBut = true;
      Serial.println("le bouton est appuyé");
      digitalWrite(pin_led, HIGH);
      if (bouton_appuye != bouton_appuye_previous) {
        bouton_appuye_previous = bouton_appuye;
        delay(250);
      }
    }
    
    if (!bouton_appuye) {
      Serial.println("le bouton est relaché");
      digitalWrite(pin_led, LOW);
      interBut = false;
      if (bouton_appuye == bouton_appuye_previous) {
        bouton_appuye_previous = !bouton_appuye;
        delay(250);
      }
    }  
    
    if (!luminosite_importante) {
      interLum = true;
      digitalWrite(pin_led2, LOW);
    }

    if (luminosite_importante) {
      digitalWrite(pin_led2, HIGH);
      digitalWrite(pin_relay, HIGH);
      Serial.println("la lumiere est trop importante");
      if (!bouton_appuye) {
        etat_lumiere = false;
      }
      interLum = false;

    }
    
    if ((interLum || interBut)&& !soiree) {

      if (mesure_ultrasons < distance_detection_ultrasonic && !cambriolage) {
        etat_capteur_ultrason = true;
      } else if (etat_capteur_ultrason && mesure_ultrasons > distance_detection_ultrasonic) {       //boucle if pour recreer bouton poussoir avec le capteur ultrasons (etat_lumière passe de true a false)
        etat_capteur_ultrason = false;
        etat_lumiere = !etat_lumiere; 
        delai = true;
      }
    }

    if (etat_lumiere) {               //boucle qui gere l'allumage et l'exctinction de la lumière
      digitalWrite(pin_relay, LOW);
      Serial.println("relay on");
    } else {
      digitalWrite(pin_relay, HIGH);
      Serial.println("relay off");
    }

    //********************partie avec les variables de l'application*************************************//

    if (cambriolage) {

      if (mesure_ultrasons < 100) {
        cambriolageDetect = true;
      }

      if (cambriolageDetect) {
        notif_state = true;
        if (millis() - previous_delay > delay_cambriolage) {
          previous_delay = millis();
          digitalWrite(pin_relay, varLum ? HIGH : LOW);
          varLum = !varLum;
        }
      }

      if (notif_state && notif_state != notif_state_previous) {
        notifPub.publish("Attention quelqu'un est passé devant le capteur ultrason");
        notif_state_previous = notif_state;
      }

      cambriolage_previous = true;

    }else{
      notif_state = false;
      cambriolageDetect = false;
      varLum = false;
      notif_state_previous = false;
      if (cambriolage != cambriolage_previous) {
        notifPub.publish("Aucune alerte       ");
        cambriolage_previous = cambriolage;
      }     
    }

    if (bande_led){
    }else{
    }

    int delay_bpm = 60000/soiree_bpm; 

    if (soiree){
      if (millis() - previous_delay_bpm > delay_bpm) {
        previous_delay_bpm = millis();
        digitalWrite(pin_relay, varLum ? HIGH : LOW);
        varLum = !varLum;
      }
    }else{
      varLum = false;
    }

    if (reveil) {
      struct tm timeinfo;
      if (getLocalTime(&timeinfo, 200)) {
        Serial.printf("Date : %02d/%02d/%04d  Heure : %02d:%02d:%02d\n", timeinfo.tm_mday, timeinfo.tm_mon + 1, timeinfo.tm_year + 1900, timeinfo.tm_hour, timeinfo.tm_min, timeinfo.tm_sec);
        if (!reveilLum && timeinfo.tm_hour == reveil_heure && timeinfo.tm_min == reveil_minute) { 
          reveilLum = true;
          digitalWrite(pin_relay, HIGH);
          etat_lumiere = true;
          lampePub.publish("ON");
          Serial.println("relay on par reveil");
        }    
      } else {
        Serial.println("Impossible d'obtenir l'heure via NTP1");
      }
    }else{
      reveilLum = false;
    }
    
    struct tm timeinfo_reset;
    if (getLocalTime(&timeinfo_reset, 200)) {
      if (timeinfo_reset.tm_hour == 0 && timeinfo_reset.tm_min == 0) {
        reveilLum = false;
      }    
    } else {
      Serial.println("Impossible d'obtenir l'heure via NTP2");
    }
  }
}     
    
  

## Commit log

2026-03-22 Update README with assembly instructions and corrections
    Corrected text regarding screwdriver types and added a new section for assembly instructions, including a table of components and their connections.
2026-03-23 final add
    jespere walla c fini
    [eco-light.stl, eco-light_fusion360.f3d]
2026-03-30 Fix ESP32 code file path in README
    Corrected the file path for the ESP32 code in the instructions.
2026-03-30 Fix code filename in README.md
    Corrected the filename for the ESP32 code in the instructions.
2026-05-18 Update ESP32 code link in README
